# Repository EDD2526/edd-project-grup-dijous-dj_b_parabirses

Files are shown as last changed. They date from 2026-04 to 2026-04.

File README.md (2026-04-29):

# Projecte DJ_B_PARABRISAS

>**Autors:Héctor Rodriguez y MariPaz Carreño
>**Versió: VFinal

----------

## Objectiu

>Crear un pcb para un limpia parabrisas, la cual tendrá control a través de un microcontrolador.
EL objetivo principal es  mantener  la luna del cristal limpia, para ello tenemos un sensor de lluvia que detectará la lluvia, un calefactor para que no se empañe, y bombas de agua que permitan en todo momento limpiar la luna.

## Diagrama de blocs
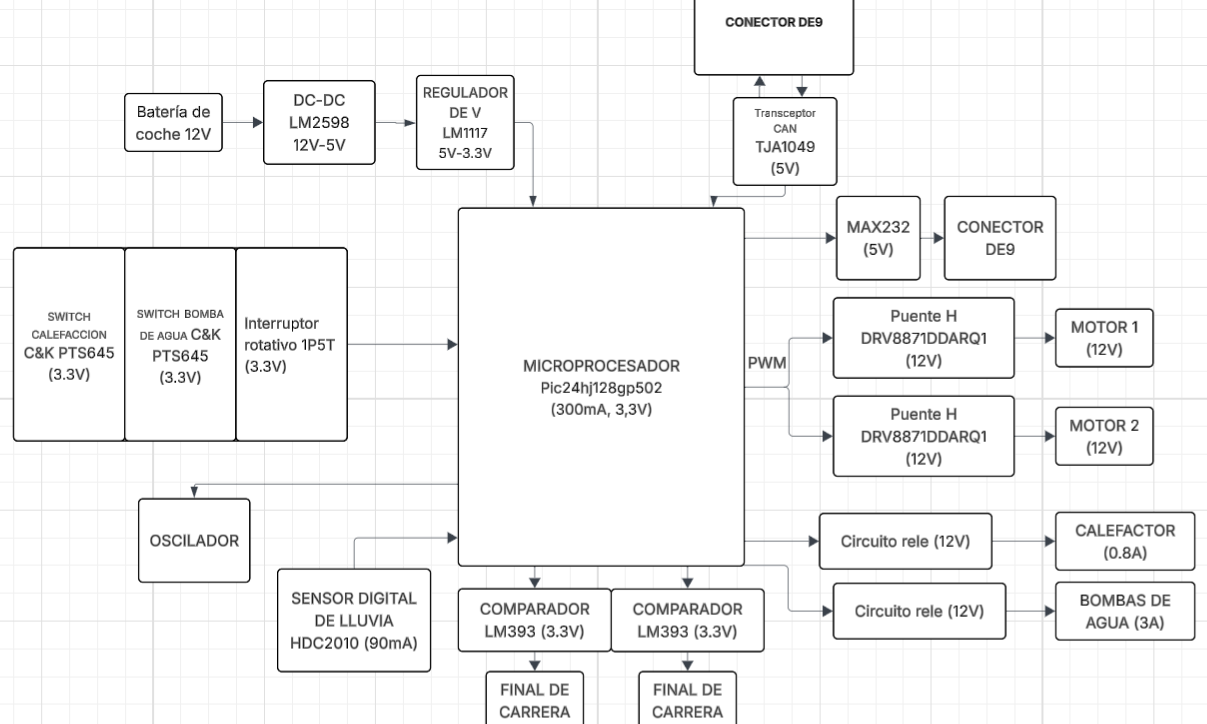
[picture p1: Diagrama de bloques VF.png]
Diagrama de bloques


### Descripció/funcionalitat de cada bloc

  Tenemos el micro en el centro que funcionará como cerebro de todo.
  Como se puede observar uno de los sería la alimentación, consta de un conector que permite meter 12V, después pasa por un convertidor        
  DC-DC, para obtener 5V y por último un regulador para tener un voltaje de 3V.
  Por otro lado tenemos el bloque de potencia: consta de los drivers y motores de los limpiaparabrisas, de los circuitos relé tanto para 
  las bombas, como para el calefactor, y de finales de carrera que permitan volver a su estado inicial.   
  Por último un bloque de conexión/usuario: consta del BUS CAN, este permite la comunicación con otros módulos, el UART, transforma los 
  datos de forma que puedan ser leídos/enviados a un ordenador. También esta el sensor digital de lluvia que detecta cuando hay lluvia y 
  que el motor se ponga en marcha, y por último tendríamos la botonera: sirve para que el usuario acomode el modo del limpiaparabrisas o 
  encienda y apague el calefactor.       
  
-----------

## Requisits / Especificacions

* Alimentació: 12V d’entrada, regulada a 5V i 3.3V
* Microcontrolador: PIC24HJ64GP504
* Regulador buck: LM2596S-5 per obtenir 5V
* Regulador LDO: LM1117DT-3.3 per obtenir 3.3V
* Protecció d’entrada: díode TVS SM6T24A
* Díodes de protecció: D4, D5 i D6 per protegir contra pics inductius
* Comunicació CAN: transceptor TJA1049TK-3
* Comunicació RS232: MAX232
* Oscil·lador: cristall Y1 
* Condensadors de desacoblament: 100nF i 1uF
* Condensadors de filtratge: 680uF, 220uF, 100uF i 10uF
* Resistències: valors diversos per polarització, pull-up, pull-down i limitació de corrent
* Punts de test: TP1, TP2 i TP3

-----------

## Components

| Descripció | Ref | Package | Datasheet | Proveïdor | Preu | Unitats |
|---|---|---|---|---|---|---|
| Capacitor 100nF | C1,C2,C10,C16 | 0805 | ~ | Mouser | — | 4 |
| Capacitor 20pF | C3,C4 | 0805 | ~ | Mouser | — | 2 |
| Capacitor 1uF | C5,C6,C7,C8,C9 | 0805 | ~ | Mouser | — | 5 |
| Capacitor 680uF | C11 | 0805 | ~ | Mouser | — | 1 |
| Capacitor 220uF | C12 | 0805 | ~ | Mouser | — | 1 |
| Capacitor 10uF | C13,C14 | CP Radial D5.0mm P2.50mm | — | Mouser | — | 2 |
| Capacitor 100uF | C15 | CP Radial D5.0mm P2.50mm | — | Mouser | — | 1 |
| Capacitor 10pF | C17 | 0805 | ~ | Mouser | — | 1 |
| Capacitor 100pF | C19 | 0805 | ~ | Mouser | — | 1 |
| LED | D2 | LED 0805 | ~ | Mouser | — | 1 |
| Diodo TVS SM6T24A | D3 | SMB | https://www.st.com/resource/en/datasheet/sm6t.pdf | Mouser | — | 1 |
| Diodo genérico | D4,D5,D6 | 0201 | ~ | Mouser | — | 3 |
| Ferrita | FB1 | LairdTech 28C0236-0JW-10 | ~ | Mouser | — | 1 |
| Final de carrera SPDT | FINALCARRERA1,FINALCARRERA2 | XKB DM1-16UC-1 | ~ | Mouser | — | 2 |
| Conector 1x05 | J1 | PinHeader 1x05 2.54mm | ~ | Mouser | — | 1 |
| Conector DE9 | J2,J3 | DSUB-9 Horizontal | ~ | Mouser | — | 2 |
| Conector 1x02 | J4 | PinHeader 1x02 2.54mm | ~ | Mouser | — | 1 |
| Jumper 3 pines | JP1 | PinHeader 1x03 2.54mm | ~ | Mouser | — | 1 |
| Relé SPST-NO Fujitsu FTR-LYAA005x | K2,K3,K4 | Relay THT Vertical | https://www.fujitsu.com/sg/imagesgig5/ftr-ly.pdf | Mouser | — | 3 |
| Inductor 33uH | L1 | 0603 | ~ | Mouser | — | 1 |
| Motor DC / Bornera salida | M1,M2,M3,M5 | TerminalBlock 2P P5.00mm | ~ | Mouser | — | 4 |
| Transistor NPN MMBT3904 | Q2,Q3,Q4 | SOT-23 | https://www.onsemi.com/pdf/datasheet/pzt3904-d.pdf | Mouser | — | 3 |
| Resistencia 1k | R2,R3,R7,R8 | 0603 | ~ | Mouser | — | 4 |
| Resistencia 4.7k | R4,R13,R14 | 0603 | ~ | Mouser | — | 3 |
| Resistencia 121Ω | R5 | 0603 | ~ | Mouser | — | 1 |
| Resistencia 200Ω | R6 | 0603 | ~ | Mouser | — | 1 |
| Resistencia 10k | R9 | 0603 | ~ | Mouser | — | 1 |
| Resistencia 4.7k | R10 | 0603 | ~ | Mouser | — | 1 |
| Resistencia calefactor | R11 | 2512 | ~ | Mouser | — | 1 |
| Resistencia 60Ω | R12,R17 | 0201 | ~ | Mouser | — | 2 |
| Resistencia 10k | R15,R16 | 0603 | ~ | Mouser | — | 2 |
| Resistencia 7.6k | R18,R22,R23 | 0603 | ~ | Mouser | — | 3 |
| Resistencia 10k | R19,R20,R21 | 0201 | ~ | Mouser | — | 3 |
| Pulsador calefactor | SW1 | Alps SKRK SMD | ~ | Mouser | — | 1 |
| Pulsador bombas | SW2 | Alps SKRK SMD | ~ | Mouser | — | 1 |
| Pulsador | SW3 | Alps SKRK SMD | ~ | Mouser | — | 1 |
| Selector rotativo SP3T | SW5 | NKK NR01 THT | https://www.nkkswitches.com/pdf/NR01%20Rotaries.pdf | Mouser | — | 1 |
| Test point | TP1,TP2,TP3 | Keystone 5015 Micro Mini | ~ | Mouser | — | 3 |
| Regulador LDO 3.3V LM1117DT-3.3 | U1 | TO-252-3 | http://www.ti.com/lit/ds/symlink/lm1117.pdf | Mouser | — | 1 |
| Regulador buck 5V LM2596S-5 | U2 | TO-263-5 | http://www.ti.com/lit/ds/symlink/lm2596.pdf | Mouser | — | 1 |
| Driver motor DRV8871DDA | U3,U7 | HTSOP-8 PowerPAD | http://www.ti.com/lit/ds/symlink/drv8871.pdf | Mouser | — | 2 |
| Microcontrolador PIC24HJ64GP504 | U4 | QFN-44 7x7mm | — | Mouser | — | 1 |
| Sensor humedad/temperatura HDC2080 | U6 | Texas S-PWSON-N6 | http://www.ti.com/lit/ds/symlink/hdc2080.pdf | Mouser | — | 1 |
| Transceptor CAN TJA1049TK-3 | U8 | HVSON-8 | https://www.nxp.com/docs/en/data-sheet/TJA1049.pdf | Mouser | — | 1 |
| Transceptor RS232 MAX232 | U9 | SOIC-16 | http://www.ti.com/lit/ds/symlink/max232.pdf | Mouser | — | 1 |
| Cristal | Y1 | SMD EuroQuartz EQ161 2Pin | ~ | Mouser | — | 1 |

-----------

## Software

### Eines:

  * KiCad 9.0 o superior
  * 

### Configuraci&#243; :

  * 

### Funcionalitats:

  Gestionar el movimiento de las escobillas, el rociado del líquido limpiador mediante dos bombas y el calentamiento del sistema mediante un calefactor.
Cuando el usuario activa el mando, la PCB recibe la señal y enciende el motor del limpiaparabrisas en el modo seleccionado. También puede activar una de las dos bombas, por ejemplo una para el parabrisas delantero y otra para el cristal trasero, enviando líquido limpiador antes o durante el movimiento de las escobillas.
Además, la PCB controla el calefactor, que sirve para calentar el líquido o la zona del sistema de lavado, evitando congelación y mejorando el funcionamiento en bajas temperaturas.

-----------

## Historial de canvis

| Data | Autor | Branch | Versi&#243; | Descripci&#243; |
| --- | --- | --- | --- | --- |
|  28/03/2023 | mlopez | Master | initial commit | Primera versi&#243; d'esquem&#224;tic i selecci&#243; de components |

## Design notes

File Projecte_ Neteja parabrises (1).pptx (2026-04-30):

## Projecte: Neteja parabrises

Hèctor Rodríguez i Marypaz Carreño

## Índice

-Funcionalidad
-Objetivos
-Diagrama de bloques
-Puntos críticos
-Componentes
-PCB, Esquemático, Visión 3D
-Presupuesto

## Funcionalidad

Gestionar el movimiento de las escobillas, el rociado del líquido limpiador mediante dos bombas y el calentamiento del sistema mediante un calefactor.
Cuando el usuario activa el mando, la PCB recibe la señal y enciende el motor del limpiaparabrisas en el modo seleccionado. También puede activar una de las dos bombas, por ejemplo una para el parabrisas delantero y otra para el cristal trasero, enviando líquido limpiador antes o durante el movimiento de las escobillas.
Además, la PCB controla el calefactor, que sirve para calentar el líquido o la zona del sistema de lavado, evitando congelación y mejorando el funcionamiento en bajas temperaturas.

## Objetivos

Mantener las lunas del coche todo lo limpias posible para que el conductor pueda tener una buen visibilidad.

## Diagrama de bloques


## Puntos críticos

- Planos de alimentacion.
- Cantidad de pines para switches.
- Routing de la parte de potencia.
- Dimensiones de pista, debido a la alta corriente.

## Componentes

- Microcontrolador PIC24HJ64GP504
- Regulador buck LM2596S-5
- Regulador LDO LM1117DT-3.3
- Driver de motor DRV8871DDA
- Transceptor CAN TJA1049TK-3
- Transceptor RS232 MAX232
- Sensor HDC2080
- Relés Fujitsu FTR-LYAA005x
- Transistores MMBT3904
- Diodo TVS SM6T24A
- Diodos genéricos
- LED

- Ferrita (Ferrite Bead)
- Inductor 33uH
- Cristal
- Resistencias
- Resistencia calefactor
- Condensadores
- Pulsadores
- Selector rotativo
- Finales de carrera
- Conectores
- Jumper
- Test points
- Borneras / terminales

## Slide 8

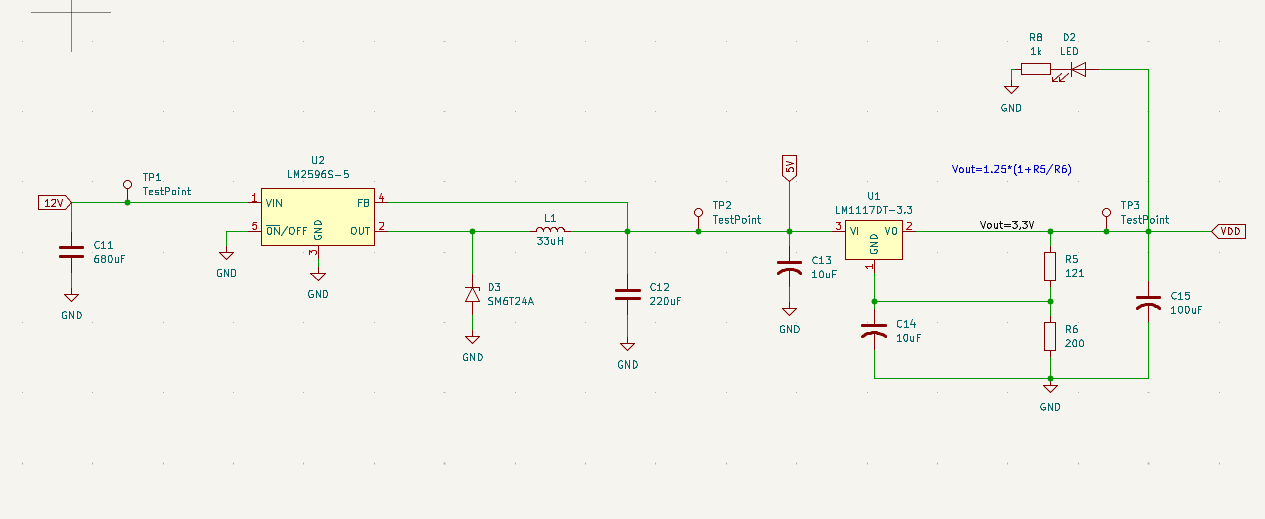
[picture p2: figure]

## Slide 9

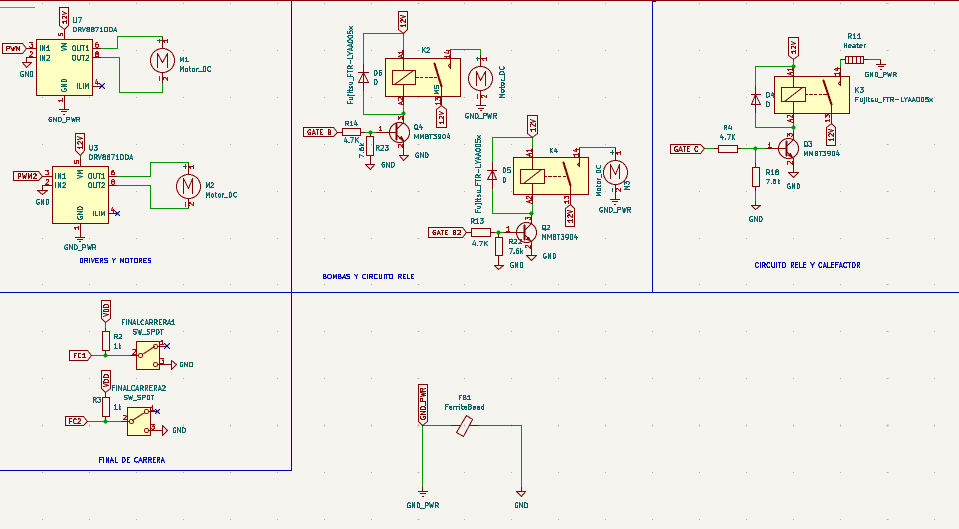
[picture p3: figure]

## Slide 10

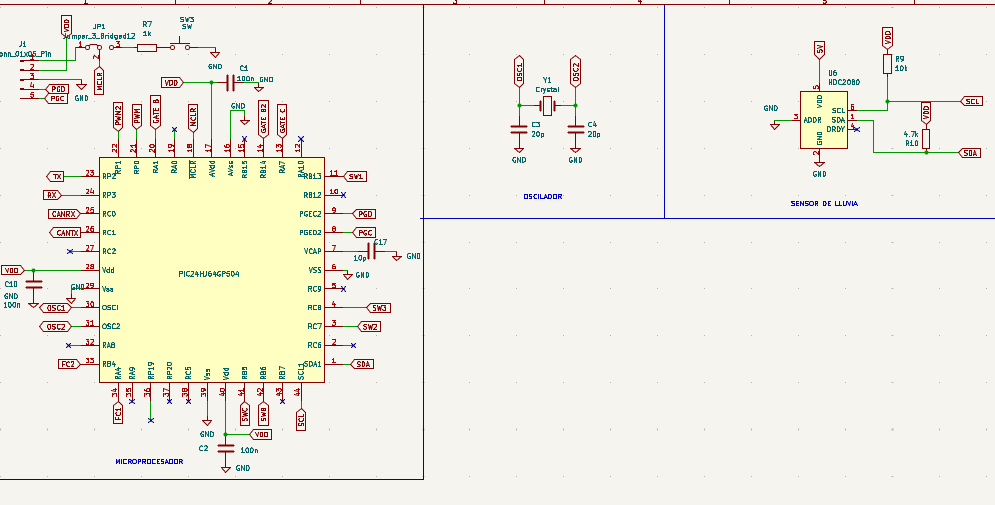
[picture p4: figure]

## BOTONERA

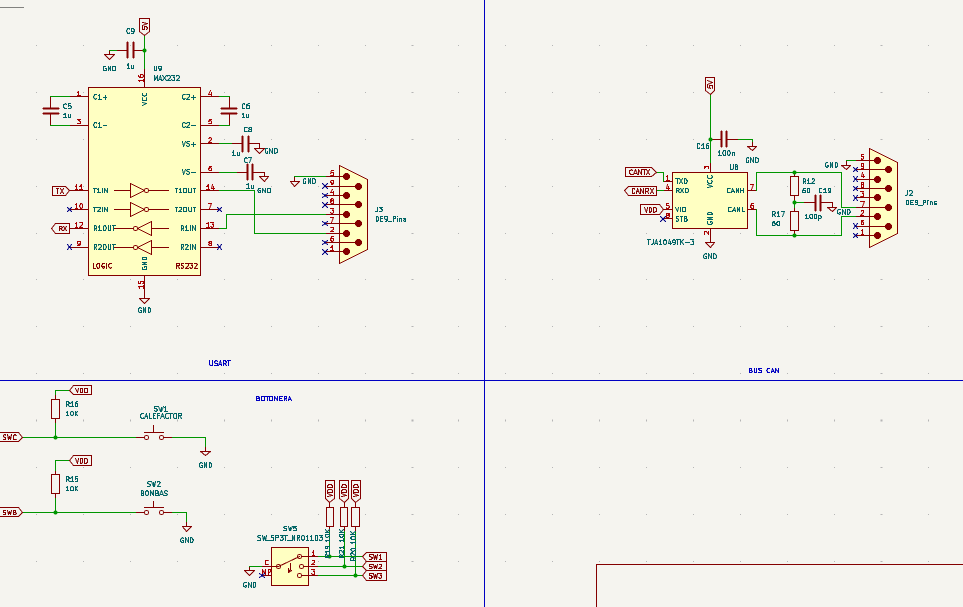
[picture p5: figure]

## PCB

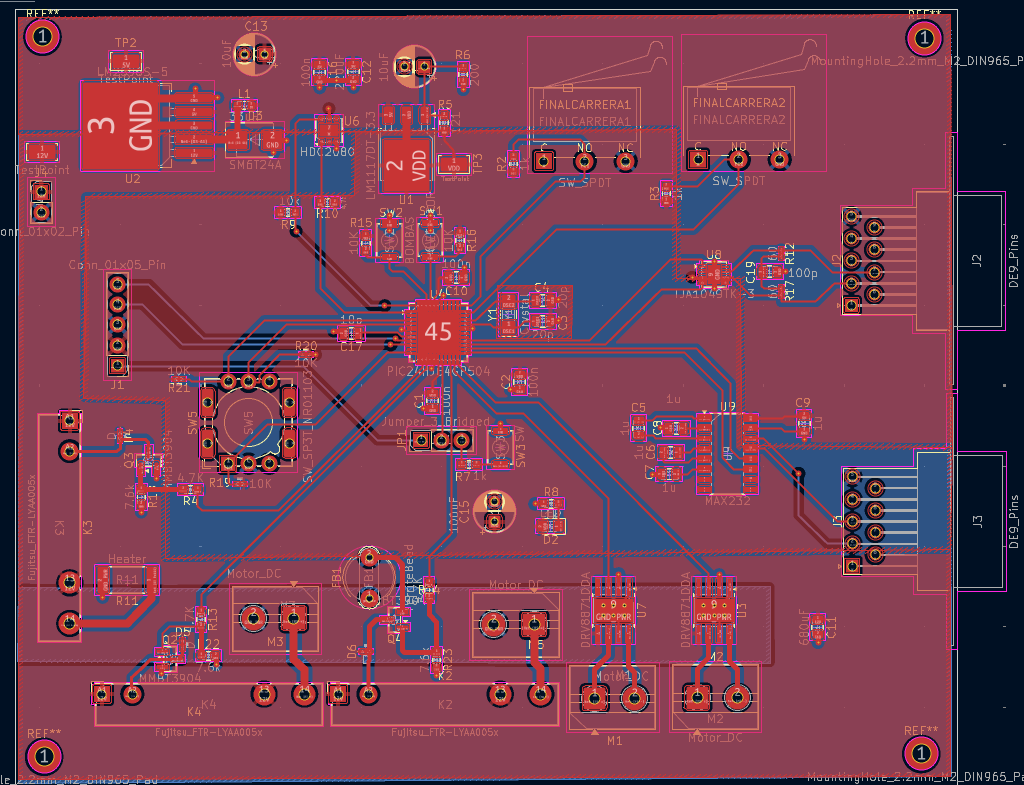
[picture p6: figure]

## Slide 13

TOP

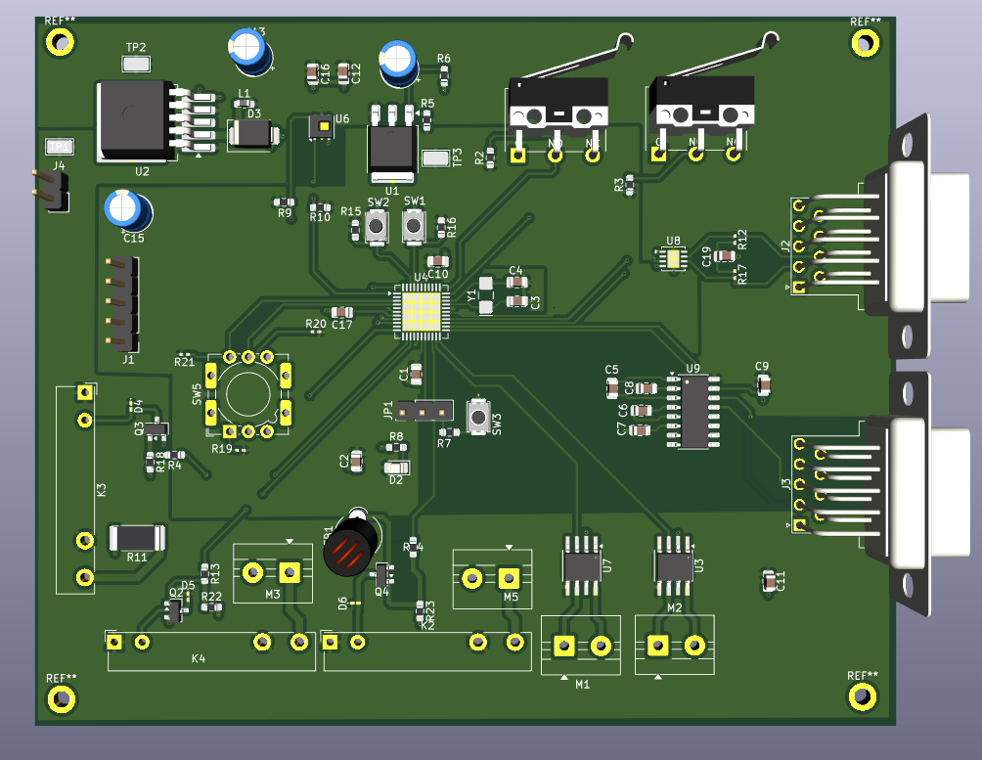
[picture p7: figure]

BOTTOM

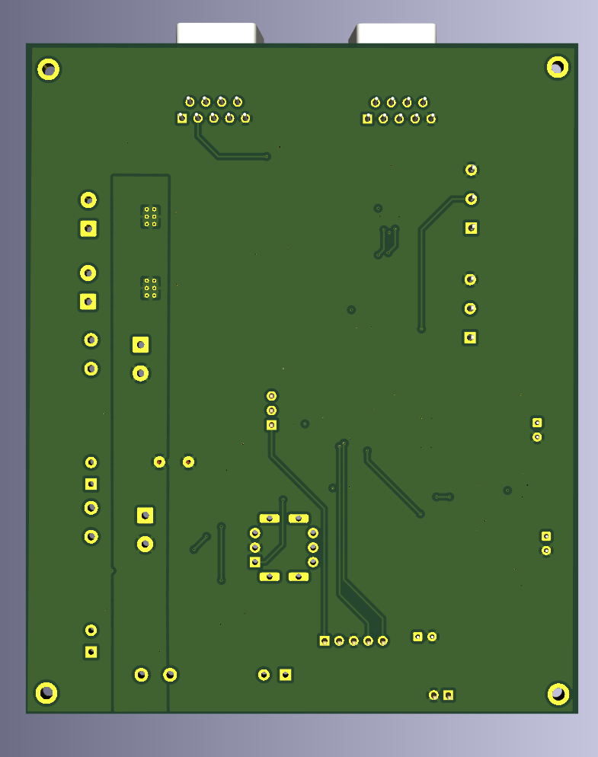
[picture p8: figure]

## Gerbers

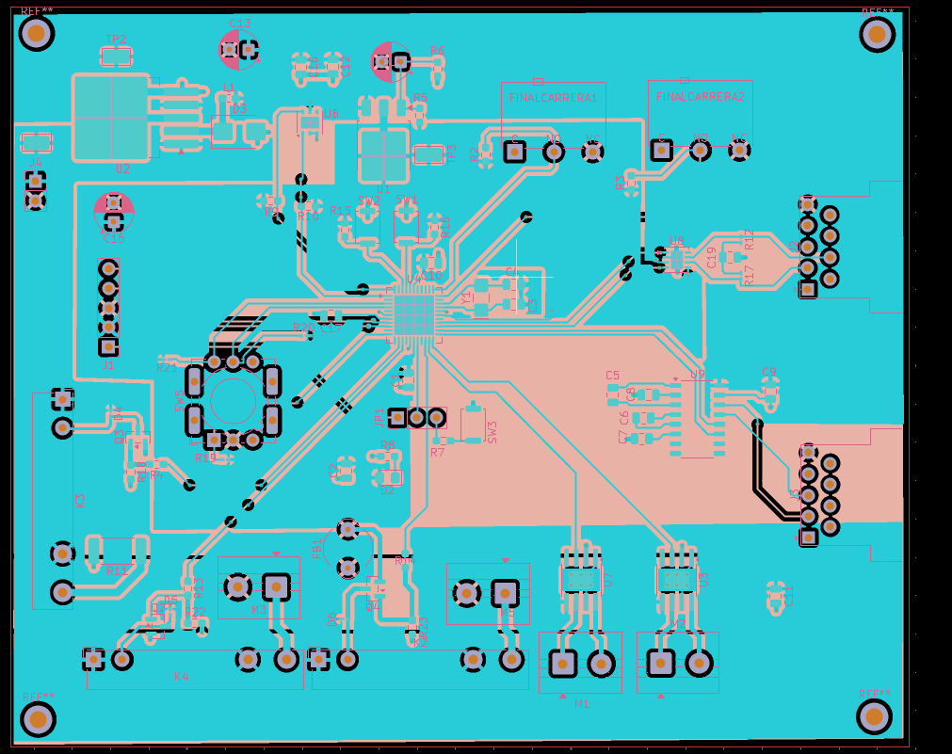
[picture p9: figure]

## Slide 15

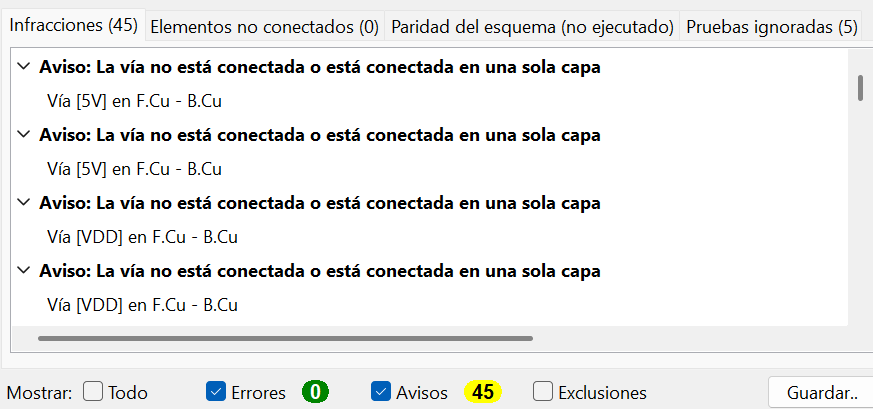
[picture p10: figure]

## Pressupost

Excel:

https://docs.google.com/spreadsheets/d/1Wet3hvXIElzK6eD7wXQeXx7nQDkMxnmVZ5MyvcNb8l4/edit?usp=sharing

Unitari: (x10)=>23.43$, (x50)=>21.8$, (x1000)=>13.14$, (x20000)=>23.59$
Total: (x10)=>234.35$, (x50)=>1090$, (x1000)=>13194$, (x20000)=>471894$

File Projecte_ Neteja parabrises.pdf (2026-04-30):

# Projecte: Neteja parabrises

Hèctor Rodríguez i Marypaz Carreño

Índice | -Funcionalidad
| -Objetivos
| -Diagrama de bloques
| -Puntos críticos
| -Componentes
| -PCB, Esquemático, Visión 3D
| -Presupuesto

# Funcionalidad

Gestionar el movimiento de las escobillas, el rociado del líquido limpiador mediante dos bombas y el calentamiento del sistema mediante un calefactor.

Cuando el usuario activa el mando, la PCB recibe la señal y enciende el motor del limpiaparabrisas en el modo seleccionado. También puede activar una de las dos bombas, por ejemplo una para el parabrisas delantero y otra para el cristal trasero, enviando líquido limpiador antes o durante el movimiento de las escobillas.

Además, la PCB controla el calefactor, que sirve para calentar el líquido o la zona del sistema de lavado, evitando congelación y mejorando el funcionamiento en bajas temperaturas.

# Objetivos

Mantener las lunas del coche todo lo limpias posible para que el conductor pueda tener una buen visibilidad.

# Diagrama de bloques

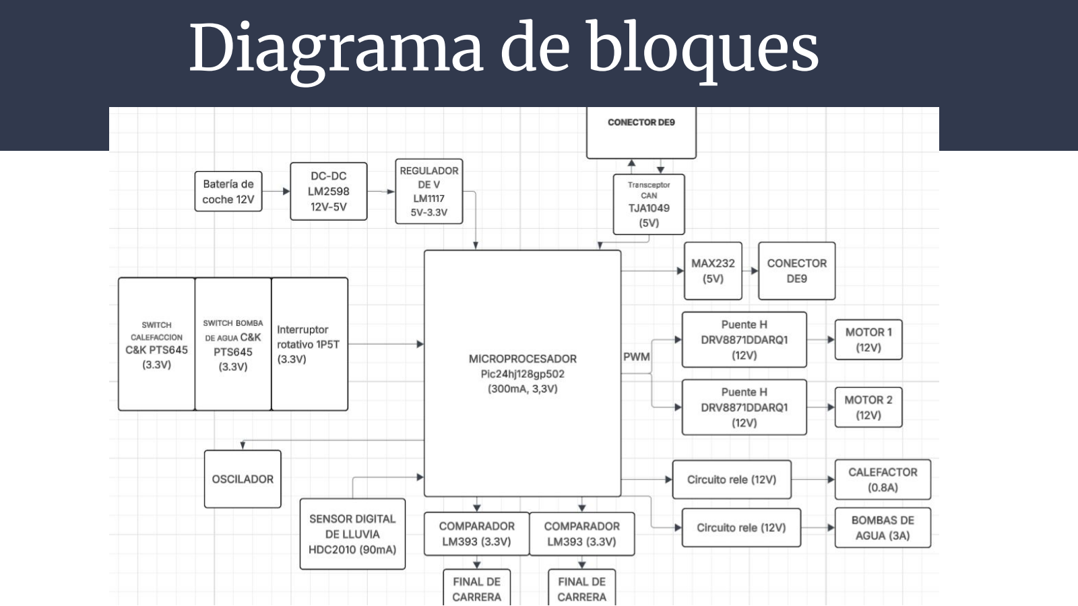
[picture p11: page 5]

# Puntos críticos

- Planos de alimentacion.
- Cantidad de pines para switches.
- Routing de la parte de potencia.
- Dimensiones de pista, debido a la alta corriente.

# Componentes

- Microcontrolador
PIC24HJ64GP504
- Regulador buck LM2596S-5
- Regulador LDO LM1117DT-3.3
- Driver de motor DRV8871DDA
- Transceptor CAN TJA1049TK-3
- Transceptor RS232 MAX232
- Sensor HDC2080
- Relés Fujitsu FTR-LYAA005x
- Transistores MMBT3904
- Diodo TVS SM6T24A
- Diodos genéricos
- LED
- Ferrita (Ferrite Bead)
- Inductor 33uH
- Cristal
- Resistencias
- Resistencia calefactor
- Condensadores
- Pulsadores
- Selector rotativo
- Finales de carrera
- Conectores
- Jumper
- Test points
- Borneras / terminales

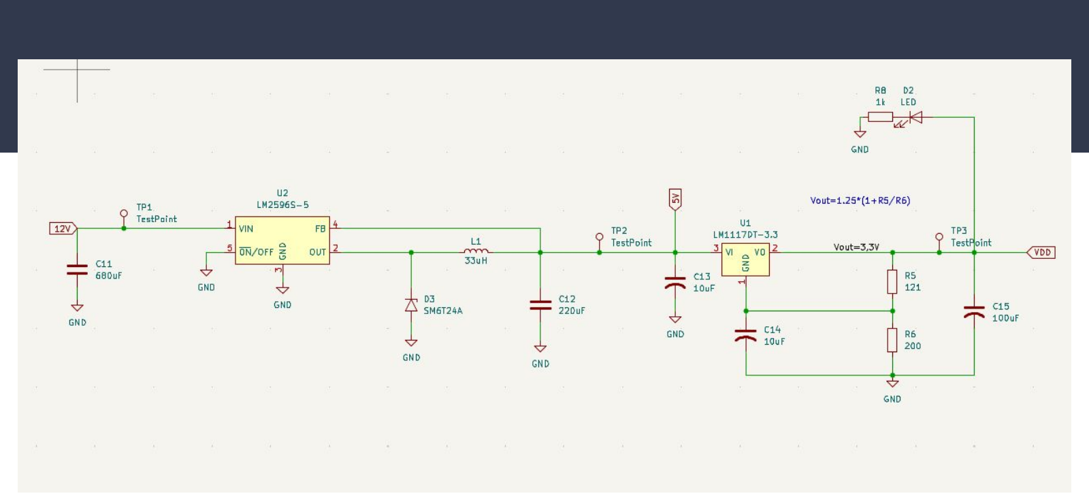
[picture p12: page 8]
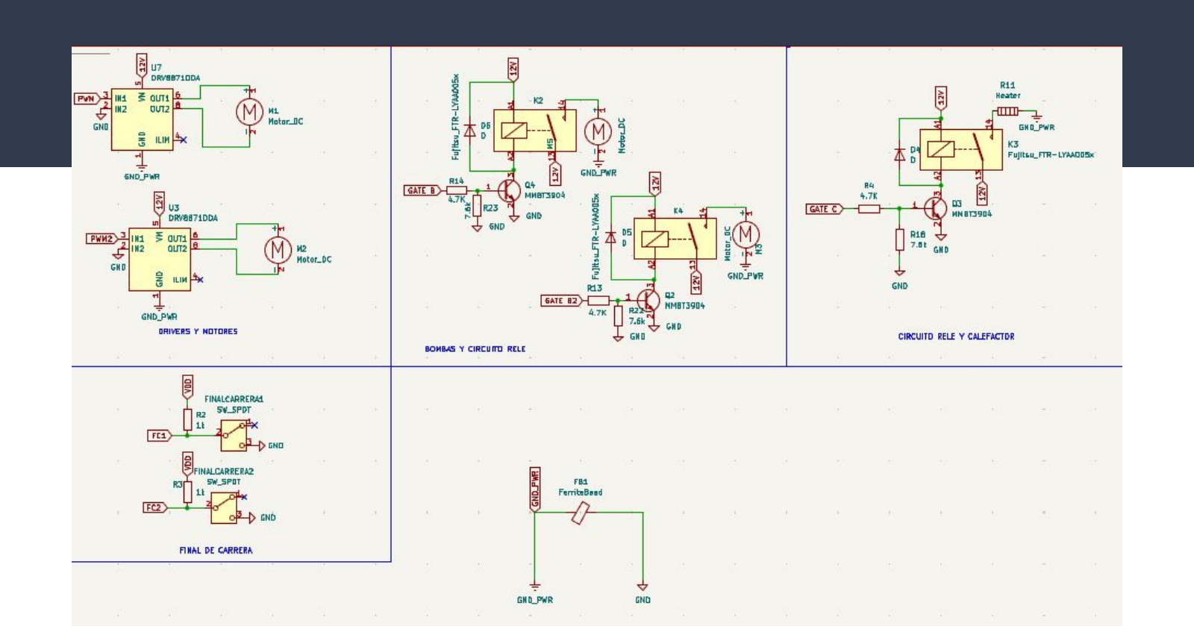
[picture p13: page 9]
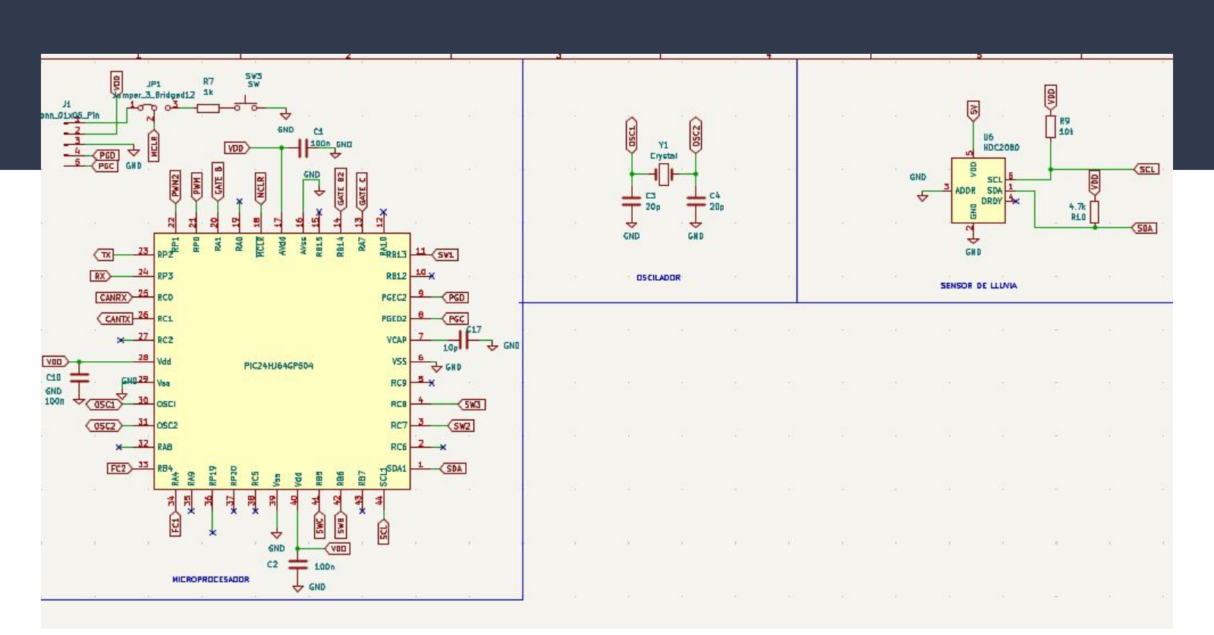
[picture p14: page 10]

## BOTONERA

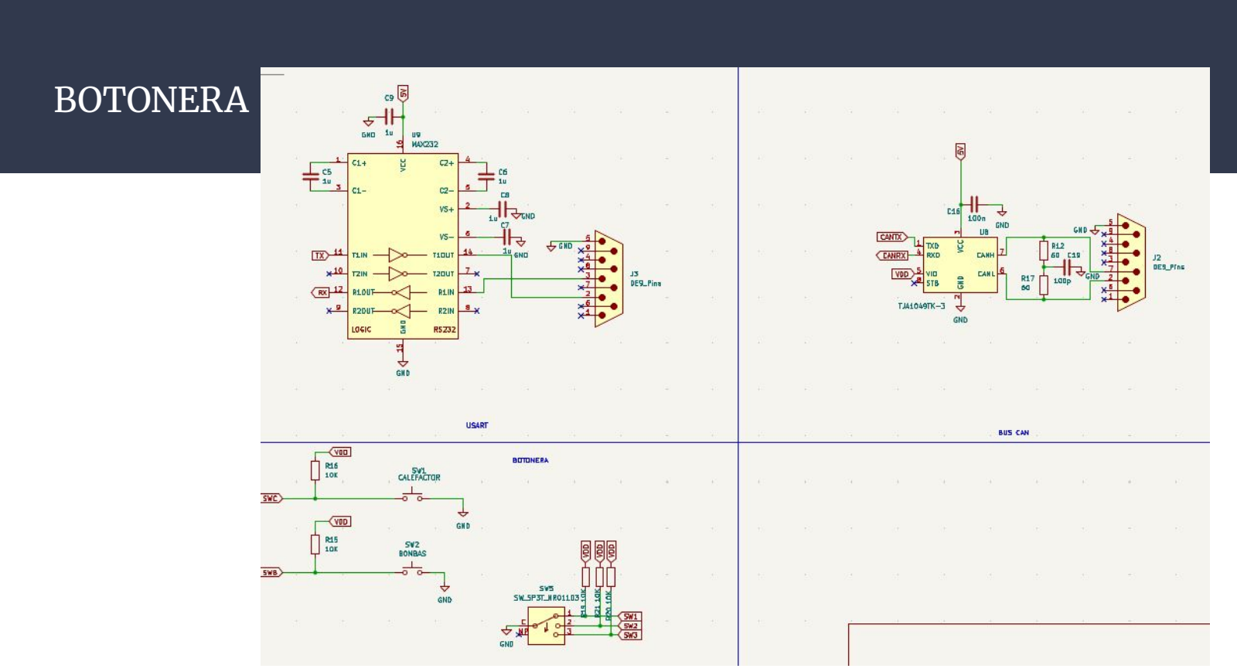
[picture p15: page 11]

# PCB

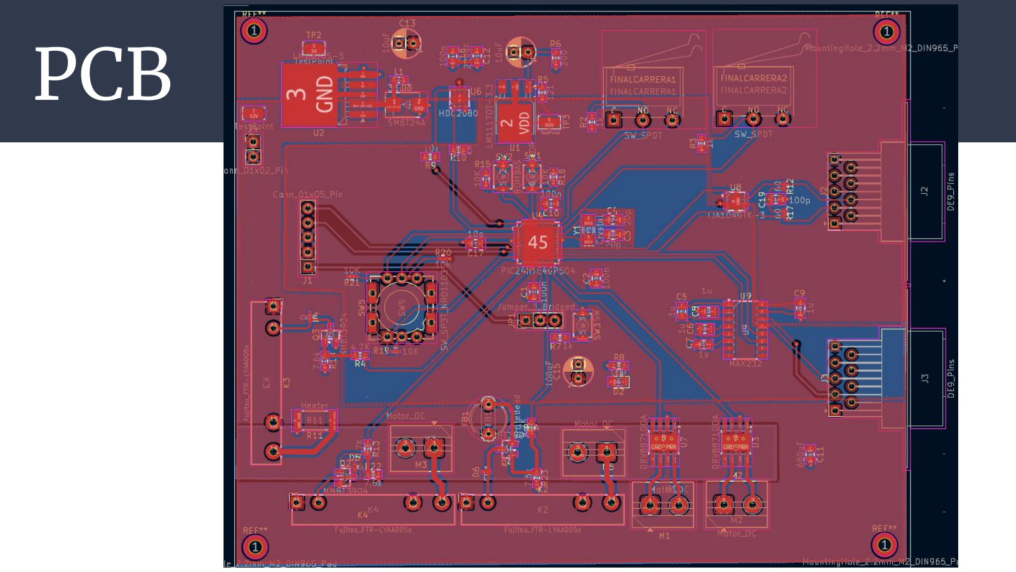
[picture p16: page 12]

TOP | BOTTOM

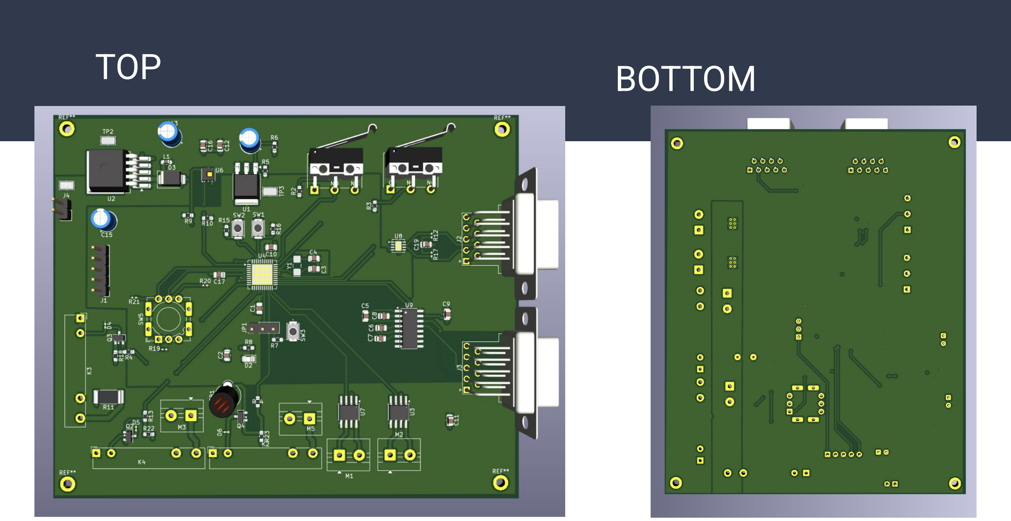
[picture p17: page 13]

# Gerbers

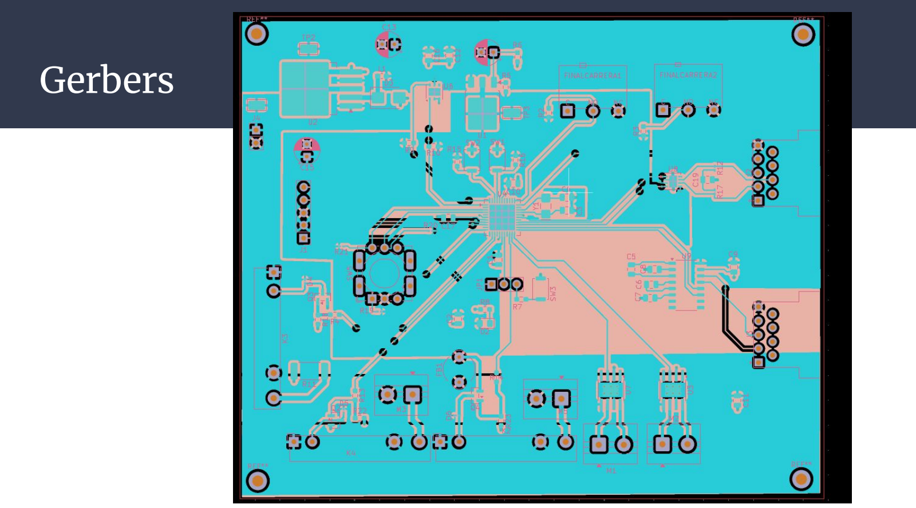
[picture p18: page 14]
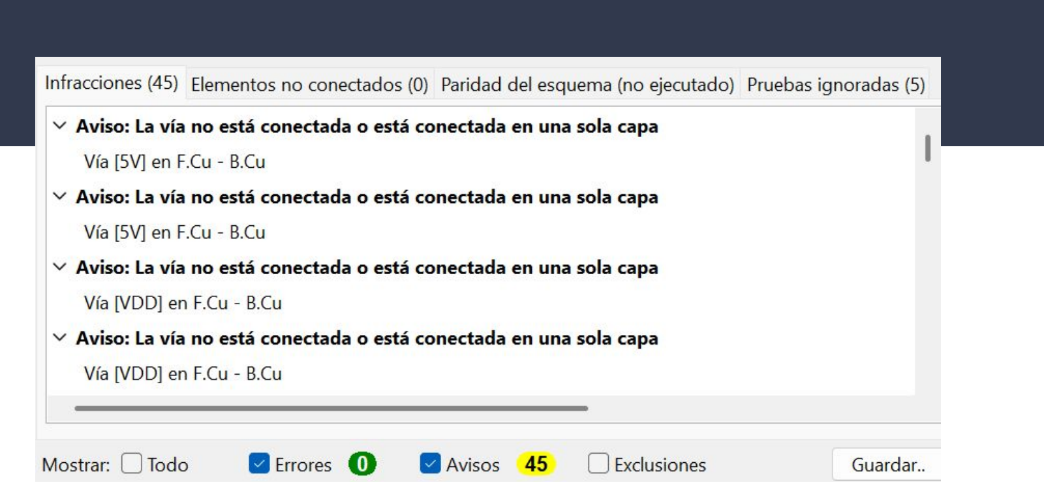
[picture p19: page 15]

# Pressupost

### Unitari: (x10)=>23.43$, (x50)=>21.8$, (x1000)=>13.14$, (x20000)=>23.59$

### Total: (x10)=>234.35$, (x50)=>1090$, (x1000)=>13194$, (x20000)=>471894$

https://docs.google.com/spreadsheets/d/1Wet3hvXIElzK6eD7wXQeXx7nQDkMxnmVZ5MyvcNb8l4/edit?usp=sharing (https://docs.google.com/spreadsheets/d/1Wet3hvXIElzK6eD7wXQeXx7nQDkMxnmVZ5MyvcNb8l4/edit?usp=sharing)

### Excel:

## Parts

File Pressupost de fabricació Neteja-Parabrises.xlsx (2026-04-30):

x10 | Preu unitari ($) | Preu total ($) | Referència | x50 | Preu unitari ($) | Preu total ($) | Referència | x1000 | Preu unitari ($) | Preu total ($) | Referència | x20000 | Preu unitari ($) | Preu total ($) | Referència
C1 | 0.0392 | 0.392 | https://www.unikeyic.com/products/ceramic-capacitors/fs051c104k4z2a/19464201.html | C1 | 0.0314 | 1.57 | https://www.unikeyic.com/products/ceramic-capacitors/fs051c104k4z2a/19464201.html | C1 | 0.0251 | 25.1 | https://www.unikeyic.com/products/ceramic-capacitors/cl21f104zbcnnnc/18680341.html | C1 | 0.0251 | 502 | https://www.unikeyic.com/products/ceramic-capacitors/cl21f104zbcnnnc/18680341.html
C2 | 0.0392 | 0.392 | https://www.unikeyic.com/products/ceramic-capacitors/fs051c104k4z2a/19464201.html | C2 | 0.0314 | 1.57 | https://www.unikeyic.com/products/ceramic-capacitors/fs051c104k4z2a/19464201.html | C2 | 0.0251 | 25.1 | https://www.unikeyic.com/products/ceramic-capacitors/cl21f104zbcnnnc/18680341.html | C2 | 0.0251 | 502 | https://www.unikeyic.com/products/ceramic-capacitors/cl21f104zbcnnnc/18680341.html
C3 | 0.245 | 2.45 | https://www.unikeyic.com/products/ceramic-capacitors/gqm2195c2e200jb12d/9406125.html | C3 | 0.245 | 12.25 | https://www.unikeyic.com/products/ceramic-capacitors/gqm2195c2e200jb12d/9406125.html | C3 | 0.0205 | 20.5 | https://www.unikeyic.com/products/ceramic-capacitors/c0805c200k8hactu/10609661.html | C3 | 0.007 | 140 | https://www.unikeyic.com/products/ceramic-capacitors/tcc0805cog200j500bt/21239242.html
C4 | 0.245 | 2.45 | https://www.unikeyic.com/products/ceramic-capacitors/gqm2195c2e200jb12d/9406125.html | C4 | 0.245 | 12.25 | https://www.unikeyic.com/products/ceramic-capacitors/gqm2195c2e200jb12d/9406125.html | C4 | 0.0205 | 20.5 | https://www.unikeyic.com/products/ceramic-capacitors/c0805c200k8hactu/10609661.html | C4 | 0.007 | 140 | https://www.unikeyic.com/products/ceramic-capacitors/tcc0805cog200j500bt/21239242.html
C5 | 0.0173 | 0.173 | https://www.unikeyic.com/products/ceramic-capacitors/cc0805mry5v7bb105/7588510.html | C5 | 0.0085 | 0.425 | https://www.unikeyic.com/products/ceramic-capacitors/ac0805kkx7r5bb105/20753629.html | C5 | 0.0073 | 7.3 | https://www.unikeyic.com/products/ceramic-capacitors/ac0805kkx7r5bb105/20753629.html | C5 | 0.0133 | 266 | https://www.unikeyic.com/products/ceramic-capacitors/cl21b105kofnfne/6708661.html
C6 | 0.0173 | 0.173 | https://www.unikeyic.com/products/ceramic-capacitors/cc0805mry5v7bb105/7588510.html | C6 | 0.0085 | 0.425 | https://www.unikeyic.com/products/ceramic-capacitors/ac0805kkx7r5bb105/20753629.html | C6 | 0.0073 | 7.3 | https://www.unikeyic.com/products/ceramic-capacitors/ac0805kkx7r5bb105/20753629.html | C6 | 0.0133 | 266 | https://www.unikeyic.com/products/ceramic-capacitors/cl21b105kofnfne/6708661.html
C7 | 0.0173 | 0.173 | https://www.unikeyic.com/products/ceramic-capacitors/cc0805mry5v7bb105/7588510.html | C7 | 0.0085 | 0.425 | https://www.unikeyic.com/products/ceramic-capacitors/ac0805kkx7r5bb105/20753629.html | C7 | 0.0073 | 7.3 | https://www.unikeyic.com/products/ceramic-capacitors/ac0805kkx7r5bb105/20753629.html | C7 | 0.0133 | 266 | https://www.unikeyic.com/products/ceramic-capacitors/cl21b105kofnfne/6708661.html
C8 | 0.0173 | 0.173 | https://www.unikeyic.com/products/ceramic-capacitors/cc0805mry5v7bb105/7588510.html | C8 | 0.0085 | 0.425 | https://www.unikeyic.com/products/ceramic-capacitors/ac0805kkx7r5bb105/20753629.html | C8 | 0.0073 | 7.3 | https://www.unikeyic.com/products/ceramic-capacitors/ac0805kkx7r5bb105/20753629.html | C8 | 0.0133 | 266 | https://www.unikeyic.com/products/ceramic-capacitors/cl21b105kofnfne/6708661.html
C9 | 0.0173 | 0.173 | https://www.unikeyic.com/products/ceramic-capacitors/cc0805mry5v7bb105/7588510.html | C9 | 0.0085 | 0.425 | https://www.unikeyic.com/products/ceramic-capacitors/ac0805kkx7r5bb105/20753629.html | C9 | 0.0073 | 7.3 | https://www.unikeyic.com/products/ceramic-capacitors/ac0805kkx7r5bb105/20753629.html | C9 | 0.0133 | 266 | https://www.unikeyic.com/products/ceramic-capacitors/cl21b105kofnfne/6708661.html
C10 | 0.0392 | 0.392 | https://www.unikeyic.com/products/ceramic-capacitors/fs051c104k4z2a/19464201.html | C10 | 0.0314 | 1.57 | https://www.unikeyic.com/products/ceramic-capacitors/fs051c104k4z2a/19464201.html | C10 | 0.0289 | 28.9 | https://www.unikeyic.com/products/ceramic-capacitors/cl21f104zbcnnnc/18680341.html | C10 | 0.0251 | 502 | https://www.unikeyic.com/products/ceramic-capacitors/cl21f104zbcnnnc/18680341.html
C11 | 0.3301 | 3.301 | https://www.unikeyic.com/products/ceramic-capacitors/sr215a681kaatr1/10381887.html | C11 | 0.3301 | 16.505 | https://www.unikeyic.com/products/ceramic-capacitors/sr215a681kaatr1/10381887.html | C11 | 0.0561 | 56.1 | https://www.unikeyic.com/products/ceramic-capacitors/0603zc681kat2a/7394239.html | C11 | 0.0198 | 396 | https://www.unikeyic.com/products/ceramic-capacitors/grm1885c1h681fa01d/20994921.html
C12 | 0.3512 | 3.512 | https://www.unikeyic.com/products/ceramic-capacitors/grm31cr60g227me11l/19408997.html | C12 | 0.2953 | 14.765 | https://www.unikeyic.com/products/ceramic-capacitors/grm31cr60g227me11l/19408997.html | C12 | 0.2436 | 243.6 | https://www.unikeyic.com/products/ceramic-capacitors/grm31cr60g227me11l/19408997.html | C12 | 0.2104 | 4208 | https://www.unikeyic.com/products/ceramic-capacitors/c1206x5r227m6r3nt/1005581067.html
C13 | 0.1428 | 1.428 | https://www.unikeyic.com/products/ceramic-capacitors/msasj21gab7106ktna01/14967858.html | C13 | 0.1428 | 7.14 | https://www.unikeyic.com/products/ceramic-capacitors/msasj21gab7106ktna01/14967858.html | C13 | 0.0566 | 56.6 | https://www.unikeyic.com/products/ceramic-capacitors/grm21bc80j106me19l/10240704.html | C13 | 0.0052 | 104 | https://www.unikeyic.com/products/ceramic-capacitors/c0805x5r106k100ns/30244845.html
C14 | 0.1428 | 1.428 | https://www.unikeyic.com/products/ceramic-capacitors/msasj21gab7106ktna01/14967858.html | C14 | 0.1428 | 7.14 | https://www.unikeyic.com/products/ceramic-capacitors/msasj21gab7106ktna01/14967858.html | C14 | 0.0566 | 56.6 | https://www.unikeyic.com/products/ceramic-capacitors/grm21bc80j106me19l/10240704.html | C14 | 0.0052 | 104 | https://www.unikeyic.com/products/ceramic-capacitors/c0805x5r106k100ns/30244845.html
C15 | 0.1792 | 1.792 | https://www.unikeyic.com/products/ceramic-capacitors/grm21br60j107me15k/19293684.html | C15 | 0.1338 | 6.69 | https://www.unikeyic.com/products/ceramic-capacitors/grm21br60j107me15k/19293684.html | C15 | 0.1145 | 114.5 | https://www.unikeyic.com/products/ceramic-capacitors/grm21br60j107me15k/19293684.html | C15 | 0.1379 | 2758 | https://www.unikeyic.com/products/ceramic-capacitors/grm21br60g107me11k/7312965.html
C16 | 0.0392 | 0.392 | https://www.unikeyic.com/products/ceramic-capacitors/fs051c104k4z2a/19464201.html | C16 | 0.0314 | 1.57 | https://www.unikeyic.com/products/ceramic-capacitors/fs051c104k4z2a/19464201.html | C16 | 0.0289 | 28.9 | https://www.unikeyic.com/products/ceramic-capacitors/cl21f104zbcnnnc/18680341.html | C16 | 0.0251 | 502 | https://www.unikeyic.com/products/ceramic-capacitors/cl21f104zbcnnnc/18680341.html
C17 | 0.0041 | 0.041 | https://www.unikeyic.com/products/ceramic-capacitors/cga0805c0g100j500ht/857497660.html | C17 | 0.0032 | 0.16 | https://www.unikeyic.com/products/ceramic-capacitors/cga0805c0g100j500ht/857497660.html | C17 | 0.0097 | 9.7 | https://www.unikeyic.com/products/ceramic-capacitors/c0805c100j5gac7800/6769988.html | C17 | 0.0052 | 104 | https://www.unikeyic.com/products/ceramic-capacitors/ac0805jrnpo9bn100/9246806.html
C19 | 0.0181 | 0.181 | https://www.unikeyic.com/products/ceramic-capacitors/08055c101jat2a/20491657.html | C19 | 0.0181 | 0.905 | https://www.unikeyic.com/products/ceramic-capacitors/08055c101jat2a/20491657.html | C19 | 0.0153 | 15.3 | https://www.unikeyic.com/products/ceramic-capacitors/c0805x7r101-101jnp/21187320.html | C19 | 0.0153 | 306 | https://www.unikeyic.com/products/ceramic-capacitors/c0805x7r101-101jnp/21187320.html
D2 | 0.0123 | 0.123 | https://www.unikeyic.com/products/led/ncd0805r1/13242756.html | D2 | 0.0122 | 0.61 | https://www.unikeyic.com/products/led/ncd0805o1/30976298.html | D2 | 0.0104 | 10.4 | https://www.unikeyic.com/products/led/ncd0805o1/30976298.html | D2 | 0.0024 | 48 | https://www.unikeyic.com/products/led/aav-004-r000/1000194485.html
D3 | 1.0792 | 10.792 | https://www.unikeyic.com/products/current-stabilizing-diodes/tlp548j-tp1-f/8251332.html | D3 | 0.8997 | 44.985 | https://www.unikeyic.com/products/current-stabilizing-diodes/tlp548j-tp1-f/8251332.html | D3 | 0.0475 | 47.5 | https://www.unikeyic.com/products/current-stabilizing-diodes/lm317/871062347.html | D3 | 0.0443 | 886 | https://www.unikeyic.com/products/current-stabilizing-diodes/lm317/871062347.html
D4 | 1.0792 | 10.792 | https://www.unikeyic.com/products/current-stabilizing-diodes/tlp548j-tp1-f/8251332.html | D4 | 0.8997 | 44.985 | https://www.unikeyic.com/products/current-stabilizing-diodes/tlp548j-tp1-f/8251332.html | D4 | 0.0475 | 47.5 | https://www.unikeyic.com/products/current-stabilizing-diodes/lm317/871062347.html | D4 | 0.0443 | 886 | https://www.unikeyic.com/products/current-stabilizing-diodes/lm317/871062347.html
D5 | 1.0792 | 10.792 | https://www.unikeyic.com/products/current-stabilizing-diodes/tlp548j-tp1-f/8251332.html | D5 | 0.8997 | 44.985 | https://www.unikeyic.com/products/current-stabilizing-diodes/tlp548j-tp1-f/8251332.html | D5 | 0.0475 | 47.5 | https://www.unikeyic.com/products/current-stabilizing-diodes/lm317/871062347.html | D5 | 0.0443 | 886 | https://www.unikeyic.com/products/current-stabilizing-diodes/lm317/871062347.html
D6 | 1.0792 | 10.792 | https://www.unikeyic.com/products/current-stabilizing-diodes/tlp548j-tp1-f/8251332.html | D6 | 0.8997 | 44.985 | https://www.unikeyic.com/products/current-stabilizing-diodes/tlp548j-tp1-f/8251332.html | D6 | 0.0475 | 47.5 | https://www.unikeyic.com/products/current-stabilizing-diodes/lm317/871062347.html | D6 | 0.0443 | 886 | https://www.unikeyic.com/products/current-stabilizing-diodes/lm317/871062347.html
FB1 | 1.0032 | 10.032 | https://www.unikeyic.com/products/magnetic-beads/28c0236-0bw-10/28061261.html | FB1 | 1.0032 | 50.16 | https://www.unikeyic.com/products/magnetic-beads/28c0236-0bw-10/28061261.html | FB1 | 0.0507 | 50.7 | https://www.unikeyic.com/products/magnetic-beads/fba04ha450bb-00/23676552.html | FB1 | 0.0396 | 792 | https://www.unikeyic.com/products/magnetic-beads/fba04ha450bb-00/23676552.html
FINALCARRERA1 | 0.1291 | 1.291 | https://www.unikeyic.com/products/pushbutton-switches/tk-6800-1/30582253.html | FINALCARRERA1 | 0.1062 | 5.31 | https://www.unikeyic.com/products/pushbutton-switches/tk-6800-1/30582253.html | FINALCARRERA1 | 0.1003 | 100.3 | https://www.unikeyic.com/products/pushbutton-switches/xkb8080-z/29657719.html | FINALCARRERA1 | 0.6609 | 13218 | https://www.unikeyic.com/products/pushbutton-switches/tmg1-01/30003257.html
FINALCARRERA2 | 0.1291 | 1.291 | https://www.unikeyic.com/products/pushbutton-switches/tk-6800-1/30582253.html | FINALCARRERA2 | 0.1062 | 5.31 | https://www.unikeyic.com/products/pushbutton-switches/tk-6800-1/30582253.html | FINALCARRERA2 | 0.1003 | 100.3 | https://www.unikeyic.com/products/pushbutton-switches/xkb8080-z/29657719.html | FINALCARRERA2 | 0.6609 | 13218 | https://www.unikeyic.com/products/pushbutton-switches/tmg1-01/30003257.html
J1 | 0.0542 | 0.542 | https://www.unikeyic.com/products/blade-connector-housings/0351510210/34594861.html | J1 | 0.0437 | 2.185 | https://www.unikeyic.com/products/blade-connector-housings/0351510210/34594861.html | J1 | 0.036 | 36 | https://www.unikeyic.com/products/blade-connector-housings/0351500200/18454904.html | J1 | 0.0385 | 770 | https://www.unikeyic.com/products/blade-connector-housings/351500100/19714676.html
J2 | 0.0542 | 0.542 | https://www.unikeyic.com/products/blade-connector-housings/0351510210/34594861.html | J2 | 0.0437 | 2.185 | https://www.unikeyic.com/products/blade-connector-housings/0351510210/34594861.html | J2 | 0.036 | 36 | https://www.unikeyic.com/products/blade-connector-housings/0351500200/18454904.html | J2 | 0.0385 | 770 | https://www.unikeyic.com/products/blade-connector-housings/351500100/19714676.html
J3 | 0.0542 | 0.542 | https://www.unikeyic.com/products/blade-connector-housings/0351510210/34594861.html | J3 | 0.0437 | 2.185 | https://www.unikeyic.com/products/blade-connector-housings/0351510210/34594861.html | J3 | 0.036 | 36 | https://www.unikeyic.com/products/blade-connector-housings/0351500200/18454904.html | J3 | 0.0385 | 770 | https://www.unikeyic.com/products/blade-connector-housings/351500100/19714676.html
J4 | 0.0542 | 0.542 | https://www.unikeyic.com/products/blade-connector-housings/0351510210/34594861.html | J4 | 0.0437 | 2.185 | https://www.unikeyic.com/products/blade-connector-housings/0351510210/34594861.html | J4 | 0.036 | 36 | https://www.unikeyic.com/products/blade-connector-housings/0351500200/18454904.html | J4 | 0.0385 | 770 | https://www.unikeyic.com/products/blade-connector-housings/351500100/19714676.html
JP1 | 0.0542 | 0.542 | https://www.unikeyic.com/products/blade-connector-housings/0351510210/34594861.html | JP1 | 0.0437 | 2.185 | https://www.unikeyic.com/products/blade-connector-housings/0351510210/34594861.html | JP1 | 0.036 | 36 | https://www.unikeyic.com/products/blade-connector-housings/0351500200/18454904.html | JP1 | 0.0385 | 770 | https://www.unikeyic.com/products/blade-connector-housings/351500100/19714676.html
K2 | 0.3014 | 3.014 | https://www.unikeyic.com/products/signal-relays/hk4100f-dc12v-shg/1209362.html | K2 | 0.3635 | 18.175 | https://www.unikeyic.com/products/signal-relays/hfd16-4-5-zfh3n/102142.html | K2 | 0.1885 | 188.5 | https://www.unikeyic.com/products/signal-relays/1649222-4/33950113.html | K2 | 2.6 | 52000 | https://www.unikeyic.com/products/signal-relays/v23079b1202b301/30598845.html
K3 | 0.3014 | 3.014 | https://www.unikeyic.com/products/signal-relays/hk4100f-dc12v-shg/1209362.html | K3 | 0.3635 | 18.175 | https://www.unikeyic.com/products/signal-relays/hfd16-4-5-zfh3n/102142.html | K3 | 0.1885 | 188.5 | https://www.unikeyic.com/products/signal-relays/1649222-4/33950113.html | K3 | 2.6 | 52000 | https://www.unikeyic.com/products/signal-relays/v23079b1202b301/30598845.html
K4 | 0.3014 | 3.014 | https://www.unikeyic.com/products/signal-relays/hk4100f-dc12v-shg/1209362.html | K4 | 0.3635 | 18.175 | https://www.unikeyic.com/products/signal-relays/hfd16-4-5-zfh3n/102142.html | K4 | 0.1885 | 188.5 | https://www.unikeyic.com/products/signal-relays/1649222-4/33950113.html | K4 | 2.6 | 52000 | https://www.unikeyic.com/products/signal-relays/v23079b1202b301/30598845.html
L1 | 0.1102 | 1.102 | https://www.unikeyic.com/products/power-inductors/slo0630h330mtt/28122264.html | L1 | 0.0912 | 4.56 | https://www.unikeyic.com/products/power-inductors/slo0630h330mtt/28122264.html | L1 | 0.0326 | 32.6 | https://www.unikeyic.com/products/power-inductors/sm7850-330mt/24116420.html | L1 | 0.015 | 300 | https://www.unikeyic.com/products/power-inductors/sm3521-330mt/27973129.html
M1 | 0.0358 | 0.358 | https://www.unikeyic.com/products/motor-driver/l9110s/34426605.html | M1 | 0.0296 | 1.48 | https://www.unikeyic.com/products/motor-driver/gr6212/1005575493.html | M1 | 0.0199 | 19.9 | https://www.unikeyic.com/products/motor-driver/gr6212/1005575493.html | M1 | 0.0114 | 228 | https://www.unikeyic.com/products/motor-driver/sa6208/871310652.html
M2 | 0.0358 | 0.358 | https://www.unikeyic.com/products/motor-driver/l9110s/34426605.html | M2 | 0.0296 | 1.48 | https://www.unikeyic.com/products/motor-driver/gr6212/1005575493.html | M2 | 0.0199 | 19.9 | https://www.unikeyic.com/products/motor-driver/gr6212/1005575493.html | M2 | 0.0114 | 228 | https://www.unikeyic.com/products/motor-driver/sa6208/871310652.html
M3 | 0.0358 | 0.358 | https://www.unikeyic.com/products/motor-driver/l9110s/34426605.html | M3 | 0.0296 | 1.48 | https://www.unikeyic.com/products/motor-driver/gr6212/1005575493.html | M3 | 0.0199 | 19.9 | https://www.unikeyic.com/products/motor-driver/gr6212/1005575493.html | M3 | 0.0114 | 228 | https://www.unikeyic.com/products/motor-driver/sa6208/871310652.html
M5 | 0.0358 | 0.358 | https://www.unikeyic.com/products/motor-driver/l9110s/34426605.html | M5 | 0.0296 | 1.48 | https://www.unikeyic.com/products/motor-driver/gr6212/1005575493.html | M5 | 0.0199 | 19.9 | https://www.unikeyic.com/products/motor-driver/gr6212/1005575493.html | M5 | 0.0114 | 228 | https://www.unikeyic.com/products/motor-driver/sa6208/871310652.html
Q2 | 0.005 | 0.05 | https://www.unikeyic.com/products/bjt/mmbt3904/691147421.html?sku=100300102529011 | Q2 | 0.005 | 0.25 | https://www.unikeyic.com/products/bjt/mmbt3904/691147421.html?sku=100300102529011 | Q2 | 0.003 | 3 | https://www.unikeyic.com/products/bjt/mmbt3904/691147421.html?sku=100300102529011 | Q2 | 0.0033 | 66 | https://www.unikeyic.com/products/bjt/mmbt3904/13701173.html?sku=1003001442654832
Q3 | 0.005 | 0.05 | https://www.unikeyic.com/products/bjt/mmbt3904/691147421.html?sku=100300102529011 | Q3 | 0.005 | 0.25 | https://www.unikeyic.com/products/bjt/mmbt3904/691147421.html?sku=100300102529011 | Q3 | 0.003 | 3 | https://www.unikeyic.com/products/bjt/mmbt3904/691147421.html?sku=100300102529011 | Q3 | 0.0033 | 66 | https://www.unikeyic.com/products/bjt/mmbt3904/13701173.html?sku=1003001442654832
Q4 | 0.005 | 0.05 | https://www.unikeyic.com/products/bjt/mmbt3904/691147421.html?sku=100300102529011 | Q4 | 0.005 | 0.25 | https://www.unikeyic.com/products/bjt/mmbt3904/691147421.html?sku=100300102529011 | Q4 | 0.003 | 3 | https://www.unikeyic.com/products/bjt/mmbt3904/691147421.html?sku=100300102529011 | Q4 | 0.0033 | 66 | https://www.unikeyic.com/products/bjt/mmbt3904/13701173.html?sku=1003001442654832
R2 | 0.0008 | 0.008 | https://www.unikeyic.com/products/surface-mount-resistors/wr06x102jtl/27213648.html | R2 | 0.0006 | 0.03 | https://www.unikeyic.com/products/surface-mount-resistors/scr0603f1k/1464257.html | R2 | 0.0005 | 0.5 | https://www.unikeyic.com/products/surface-mount-resistors/scr0603f1k/1464257.html | R2 | 0.0006 | 12 | https://www.unikeyic.com/products/surface-mount-resistors/rms06jt102/23527918.html
R3 | 0.0008 | 0.008 | https://www.unikeyic.com/products/surface-mount-resistors/wr06x102jtl/27213648.html | R3 | 0.0006 | 0.03 | https://www.unikeyic.com/products/surface-mount-resistors/scr0603f1k/1464257.html | R3 | 0.0005 | 0.5 | https://www.unikeyic.com/products/surface-mount-resistors/scr0603f1k/1464257.html | R3 | 0.0006 | 12 | https://www.unikeyic.com/products/surface-mount-resistors/rms06jt102/23527918.html
R4 | 0.0039 | 0.039 | https://www.unikeyic.com/products/surface-mount-resistors/rk73b1jttd472g/30481446.html | R4 | 0.1495 | 7.475 | https://www.unikeyic.com/products/surface-mount-resistors/crt0603-fx-4701elf/6691641.html | R4 | 0.001 | 1 | https://www.unikeyic.com/products/surface-mount-resistors/rc0603fr-074k7l/5502613.html | R4 | 0.0007 | 14 | https://www.unikeyic.com/products/surface-mount-resistors/rc0603fr-074k7l/5502613.html
R5 | 0.0023 | 0.023 | https://www.unikeyic.com/products/surface-mount-resistors/rc0603fr-13121rl/1596587.html | R5 | 0.0023 | 0.115 | https://www.unikeyic.com/products/surface-mount-resistors/rc0603fr-13121rl/1596587.html | R5 | 0.0023 | 2.3 | https://www.unikeyic.com/products/surface-mount-resistors/rc0603fr-13121rl/1596587.html | R5 | 0.0023 | 46 | https://www.unikeyic.com/products/surface-mount-resistors/rc0603fr-13121rl/1596587.html
R6 | 0.0012 | 0.012 | https://www.unikeyic.com/products/surface-mount-resistors/mr06x2000ftl/34104715.html | R6 | 0.0012 | 0.06 | https://www.unikeyic.com/products/surface-mount-resistors/mr06x2000ftl/34104715.html | R6 | 0.0019 | 1.9 | https://www.unikeyic.com/products/surface-mount-resistors/ac0603fr-07200rl/29991689.html | R6 | 0.0012 | 24 | https://www.unikeyic.com/products/surface-mount-resistors/cq03waj0201t5e/683918389.html
R7 | 0.0008 | 0.008 | https://www.unikeyic.com/products/surface-mount-resistors/wr06x102jtl/27213648.html | R7 | 0.0006 | 0.03 | https://www.unikeyic.com/products/surface-mount-resistors/scr0603f1k/1464257.html | R7 | 0.0005 | 0.5 | https://www.unikeyic.com/products/surface-mount-resistors/scr0603f1k/1464257.html | R7 | 0.0006 | 12 | https://www.unikeyic.com/products/surface-mount-resistors/rms06jt102/23527918.html
R8 | 0.0008 | 0.008 | https://www.unikeyic.com/products/surface-mount-resistors/wr06x102jtl/27213648.html | R8 | 0.0006 | 0.03 | https://www.unikeyic.com/products/surface-mount-resistors/scr0603f1k/1464257.html | R8 | 0.0005 | 0.5 | https://www.unikeyic.com/products/surface-mount-resistors/scr0603f1k/1464257.html | R8 | 0.0006 | 12 | https://www.unikeyic.com/products/surface-mount-resistors/rms06jt102/23527918.html
R9 | 0.033 | 0.33 | https://www.unikeyic.com/products/surface-mount-resistors/ptfr0603b10k0p9/2937877.html | R9 | 0.0273 | 1.365 | https://www.unikeyic.com/products/surface-mount-resistors/ar03btcx1002/28478659.html | R9 | 0.003 | 3 | https://www.unikeyic.com/products/surface-mount-resistors/cr0603-16w-103jt/2487102.html | R9 | 0.003 | 60 | https://www.unikeyic.com/products/surface-mount-resistors/cr0603-16w-103jt/2487102.html
R10 | 0.0039 | 0.039 | https://www.unikeyic.com/products/surface-mount-resistors/rk73b1jttd472g/30481446.html | R10 | 0.1495 | 7.475 | https://www.unikeyic.com/products/surface-mount-resistors/crt0603-fx-4701elf/6691641.html | R10 | 0.001 | 1 | https://www.unikeyic.com/products/surface-mount-resistors/rc0603fr-074k7l/5502613.html | R10 | 0.0007 | 14 | https://www.unikeyic.com/products/surface-mount-resistors/rc0603fr-074k7l/5502613.html
R11 | 1.1654 | 11.654 | https://www.unikeyic.com/products/fans-and-thermal-management/ick-smd-c-10-sa/19099179.html | R11 | 1.1192 | 55.96 | https://www.unikeyic.com/products/fans-and-thermal-management/ick-smd-c-10-sa/19099179.html | R11 | 0.4331 | 433.1 | https://www.unikeyic.com/products/fans-and-thermal-management/thjp0805ast1/22262489.html | R11 | 0.46 | 9200 | https://www.unikeyic.com/products/fans-and-thermal-management/573100d00010g/20312133.html
R12 | 0.0224 | 0.224 | https://www.unikeyic.com/products/surface-mount-resistors/esr03ezpf60r4/26629815.html | R12 | 0.0207 | 1.035 | https://www.unikeyic.com/products/surface-mount-resistors/rt0603brd0760r4l/29063300.html | R12 | 0.0016 | 1.6 | https://www.unikeyic.com/products/surface-mount-resistors/ac0603fr-0760r4l/33884214.html | R12 | 0.0013 | 26 | https://www.unikeyic.com/products/surface-mount-resistors/ac0603fr-0760r4l/33884214.html
R13 | 0.0039 | 0.039 | https://www.unikeyic.com/products/surface-mount-resistors/rk73b1jttd472g/30481446.html | R13 | 0.1495 | 7.475 | https://www.unikeyic.com/products/surface-mount-resistors/crt0603-fx-4701elf/6691641.html | R13 | 0.001 | 1 | https://www.unikeyic.com/products/surface-mount-resistors/rc0603fr-074k7l/5502613.html | R13 | 0.0007 | 14 | https://www.unikeyic.com/products/surface-mount-resistors/rc0603fr-074k7l/5502613.html
R14 | 0.0039 | 0.039 | https://www.unikeyic.com/products/surface-mount-resistors/rk73b1jttd472g/30481446.html | R14 | 0.1495 | 7.475 | https://www.unikeyic.com/products/surface-mount-resistors/crt0603-fx-4701elf/6691641.html | R14 | 0.001 | 1 | https://www.unikeyic.com/products/surface-mount-resistors/rc0603fr-074k7l/5502613.html | R14 | 0.0007 | 14 | https://www.unikeyic.com/products/surface-mount-resistors/rc0603fr-074k7l/5502613.html
R15 | 0.033 | 0.33 | https://www.unikeyic.com/products/surface-mount-resistors/ptfr0603b10k0p9/2937877.html | R15 | 0.0273 | 1.365 | https://www.unikeyic.com/products/surface-mount-resistors/ar03btcx1002/28478659.html | R15 | 0.003 | 3 | https://www.unikeyic.com/products/surface-mount-resistors/cr0603-16w-103jt/2487102.html | R15 | 0.003 | 60 | https://www.unikeyic.com/products/surface-mount-resistors/cr0603-16w-103jt/2487102.html
R16 | 0.033 | 0.33 | https://www.unikeyic.com/products/surface-mount-resistors/ptfr0603b10k0p9/2937877.html | R16 | 0.0273 | 1.365 | https://www.unikeyic.com/products/surface-mount-resistors/ar03btcx1002/28478659.html | R16 | 0.003 | 3 | https://www.unikeyic.com/products/surface-mount-resistors/cr0603-16w-103jt/2487102.html | R16 | 0.003 | 60 | https://www.unikeyic.com/products/surface-mount-resistors/cr0603-16w-103jt/2487102.html
R17 | 0.0224 | 0.224 | https://www.unikeyic.com/products/surface-mount-resistors/esr03ezpf60r4/26629815.html | R17 | 0.0207 | 1.035 | https://www.unikeyic.com/products/surface-mount-resistors/rt0603brd0760r4l/29063300.html | R17 | 0.0016 | 1.6 | https://www.unikeyic.com/products/surface-mount-resistors/ac0603fr-0760r4l/33884214.html | R17 | 0.0013 | 26 | https://www.unikeyic.com/products/surface-mount-resistors/ac0603fr-0760r4l/33884214.html
R18 | 0.0372 | 0.372 | https://www.unikeyic.com/products/surface-mount-resistors/era-3aeb7681v/33626659.html | R18 | 0.018 | 0.9 | https://www.unikeyic.com/products/surface-mount-resistors/rt0603brd077k68l/27672674.html | R18 | 0.0014 | 1.4 | https://www.unikeyic.com/products/surface-mount-resistors/ac0603fr-077k68l/9459382.html | R18 | 0.0011 | 22 | https://www.unikeyic.com/products/surface-mount-resistors/ac0603fr-077k68l/9459382.html
R19 | 0.033 | 0.33 | https://www.unikeyic.com/products/surface-mount-resistors/ptfr0603b10k0p9/2937877.html | R19 | 0.0273 | 1.365 | https://www.unikeyic.com/products/surface-mount-resistors/ar03btcx1002/28478659.html | R19 | 0.003 | 3 | https://www.unikeyic.com/products/surface-mount-resistors/cr0603-16w-103jt/2487102.html | R19 | 0.003 | 60 | https://www.unikeyic.com/products/surface-mount-resistors/cr0603-16w-103jt/2487102.html
R20 | 0.033 | 0.33 | https://www.unikeyic.com/products/surface-mount-resistors/ptfr0603b10k0p9/2937877.html | R20 | 0.0273 | 1.365 | https://www.unikeyic.com/products/surface-mount-resistors/ar03btcx1002/28478659.html | R20 | 0.003 | 3 | https://www.unikeyic.com/products/surface-mount-resistors/cr0603-16w-103jt/2487102.html | R20 | 0.003 | 60 | https://www.unikeyic.com/products/surface-mount-resistors/cr0603-16w-103jt/2487102.html
R21 | 0.033 | 0.33 | https://www.unikeyic.com/products/surface-mount-resistors/ptfr0603b10k0p9/2937877.html | R21 | 0.0273 | 1.365 | https://www.unikeyic.com/products/surface-mount-resistors/ar03btcx1002/28478659.html | R21 | 0.003 | 3 | https://www.unikeyic.com/products/surface-mount-resistors/cr0603-16w-103jt/2487102.html | R21 | 0.003 | 60 | https://www.unikeyic.com/products/surface-mount-resistors/cr0603-16w-103jt/2487102.html
R22 | 0.0372 | 0.372 | https://www.unikeyic.com/products/surface-mount-resistors/era-3aeb7681v/33626659.html | R22 | 0.018 | 0.9 | https://www.unikeyic.com/products/surface-mount-resistors/rt0603brd077k68l/27672674.html | R22 | 0.0014 | 1.4 | https://www.unikeyic.com/products/surface-mount-resistors/ac0603fr-077k68l/9459382.html | R22 | 0.0011 | 22 | https://www.unikeyic.com/products/surface-mount-resistors/ac0603fr-077k68l/9459382.html
R23 | 0.0372 | 0.372 | https://www.unikeyic.com/products/surface-mount-resistors/era-3aeb7681v/33626659.html | R23 | 0.018 | 0.9 | https://www.unikeyic.com/products/surface-mount-resistors/rt0603brd077k68l/27672674.html | R23 | 0.0014 | 1.4 | https://www.unikeyic.com/products/surface-mount-resistors/ac0603fr-077k68l/9459382.html | R23 | 0.0011 | 22 | https://www.unikeyic.com/products/surface-mount-resistors/ac0603fr-077k68l/9459382.html
SW1 | 0.1291 | 1.291 | https://www.unikeyic.com/products/pushbutton-switches/tk-6800-1/30582253.html | SW1 | 0.1062 | 5.31 | https://www.unikeyic.com/products/pushbutton-switches/tk-6800-1/30582253.html | SW1 | 0.1003 | 100.3 | https://www.unikeyic.com/products/pushbutton-switches/xkb8080-z/29657719.html | SW1 | 0.6609 | 13218 | https://www.unikeyic.com/products/pushbutton-switches/tmg1-01/30003257.html
SW2 | 0.1291 | 1.291 | https://www.unikeyic.com/products/pushbutton-switches/tk-6800-1/30582253.html | SW2 | 0.1062 | 5.31 | https://www.unikeyic.com/products/pushbutton-switches/tk-6800-1/30582253.html | SW2 | 0.1003 | 100.3 | https://www.unikeyic.com/products/pushbutton-switches/xkb8080-z/29657719.html | SW2 | 0.6609 | 13218 | https://www.unikeyic.com/products/pushbutton-switches/tmg1-01/30003257.html
SW3 | 0.1291 | 1.291 | https://www.unikeyic.com/products/pushbutton-switches/tk-6800-1/30582253.html | SW3 | 0.1062 | 5.31 | https://www.unikeyic.com/products/pushbutton-switches/tk-6800-1/30582253.html | SW3 | 0.1003 | 100.3 | https://www.unikeyic.com/products/pushbutton-switches/xkb8080-z/29657719.html | SW3 | 0.6609 | 13218 | https://www.unikeyic.com/products/pushbutton-switches/tmg1-01/30003257.html
SW5 | 0.1291 | 1.291 | https://www.unikeyic.com/products/pushbutton-switches/tk-6800-1/30582253.html | SW5 | 0.1062 | 5.31 | https://www.unikeyic.com/products/pushbutton-switches/tk-6800-1/30582253.html | SW5 | 0.1003 | 100.3 | https://www.unikeyic.com/products/pushbutton-switches/xkb8080-z/29657719.html | SW5 | 0.6609 | 13218 | https://www.unikeyic.com/products/pushbutton-switches/tmg1-01/30003257.html
U1 | 0.0856 | 0.856 | https://www.unikeyic.com/products/ldo-controller/lm1117mp-3-3-tr/34334866.html?sku=1003001016206975 | U1 | 0.0681 | 3.405 | https://www.unikeyic.com/products/ldo-controller/lm1117mp-3-3-tr/34334866.html?sku=1003001016206975 | U1 | 0.0528 | 52.8 | https://www.unikeyic.com/products/ldo-controller/lm1117mp-3-3-tr/34334866.html?sku=1003001016206975 | U1 | 0.0998 | 1996 | https://www.unikeyic.com/products/ldo-controller/lm1117mpx-3-3-nopb/34021155.html?sku=1003001442151460
U2 | 0.2022 | 2.022 | https://www.unikeyic.com/products/dc-dc-controller/lm2596s-5-0/34029210.html?sku=1003001028609652 | U2 | 0.1711 | 8.555 | https://www.unikeyic.com/products/motor-driver/drv8871ddarq1/22975465.html?sku=1003001028369650 | U2 | 0.1356 | 135.6 | https://www.unikeyic.com/products/dc-dc-controller/lm2596s-5-0/34029210.html?sku=1003001028609652 | U2 | 0.2742 | 5484 | https://www.unikeyic.com/products/dc-dc-controller/lm2596s-adj/682757583.html?sku=100300107315294
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

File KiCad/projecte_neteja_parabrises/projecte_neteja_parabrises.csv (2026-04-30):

Reference | Qty | Value | DNP | Exclude from BOM | Exclude from Board | Footprint | Datasheet
C1 | 1 | 100n |  |  |  | Capacitor_SMD:C_0805_2012Metric | ~
C2 | 1 | 100n |  |  |  | Capacitor_SMD:C_0805_2012Metric | ~
C10 | 1 | 100n |  |  |  | Capacitor_SMD:C_0805_2012Metric | ~
C16 | 1 | 100n |  |  |  | Capacitor_SMD:C_0805_2012Metric | ~
C3 | 1 | 20p |  |  |  | Capacitor_SMD:C_0805_2012Metric | ~
C4 | 1 | 20p |  |  |  | Capacitor_SMD:C_0805_2012Metric | ~
C5 | 1 | 1u |  |  |  | Capacitor_SMD:C_0805_2012Metric | ~
C6 | 1 | 1u |  |  |  | Capacitor_SMD:C_0805_2012Metric | ~
C7 | 1 | 1u |  |  |  | Capacitor_SMD:C_0805_2012Metric | ~
C8 | 1 | 1u |  |  |  | Capacitor_SMD:C_0805_2012Metric | ~
C9 | 1 | 1u |  |  |  | Capacitor_SMD:C_0805_2012Metric | ~
C11 | 1 | 680uF |  |  |  | Capacitor_SMD:C_0805_2012Metric | ~
C12 | 1 | 220uF |  |  |  | Capacitor_SMD:C_0805_2012Metric | ~
C13 | 1 | 10uF |  |  |  | Capacitor_THT:CP_Radial_D5.0mm_P2.50mm
C14 | 1 | 10uF |  |  |  | Capacitor_THT:CP_Radial_D5.0mm_P2.50mm
C15 | 1 | 100uF |  |  |  | Capacitor_THT:CP_Radial_D5.0mm_P2.50mm
C17 | 1 | 10p |  |  |  | Capacitor_SMD:C_0805_2012Metric | ~
C19 | 1 | 100p |  |  |  | Capacitor_SMD:C_0805_2012Metric | ~
D2 | 1 | LED |  |  |  | LED_SMD:LED_0805_2012Metric_Pad1.15x1.40mm_HandSolder | ~
D3 | 1 | SM6T24A |  |  |  | Diode_SMD:D_SMB | https://www.st.com/resource/en/datasheet/sm6t.pdf
D4 | 1 | D |  |  |  | Diode_SMD:D_0201_0603Metric_Pad0.64x0.40mm_HandSolder | ~
D5 | 1 | D |  |  |  | Diode_SMD:D_0201_0603Metric_Pad0.64x0.40mm_HandSolder | ~
D6 | 1 | D |  |  |  | Diode_SMD:D_0201_0603Metric_Pad0.64x0.40mm_HandSolder | ~
FB1 | 1 | FerriteBead |  |  |  | Ferrite_THT:LairdTech_28C0236-0JW-10 | ~
FINALCARRERA1 | 1 | SW_SPDT |  |  |  | Button_Switch_THT:SW_XKB_DM1-16UC-1 | ~
FINALCARRERA2 | 1 | SW_SPDT |  |  |  | Button_Switch_THT:SW_XKB_DM1-16UC-1 | ~
J1 | 1 | Conn_01x05_Pin |  |  |  | Connector_PinHeader_2.54mm:PinHeader_1x05_P2.54mm_Vertical | ~
J2 | 1 | DE9_Pins |  |  |  | Connector_Dsub:DSUB-9_Pins_Horizontal_P2.77x2.84mm_EdgePinOffset9.40mm | ~
J3 | 1 | DE9_Pins |  |  |  | Connector_Dsub:DSUB-9_Pins_Horizontal_P2.77x2.84mm_EdgePinOffset9.40mm | ~
J4 | 1 | Conn_01x02_Pin |  |  |  | Connector_PinHeader_2.54mm:PinHeader_1x02_P2.54mm_Vertical | ~
JP1 | 1 | Jumper_3_Bridged12 |  | Excluded from BOM |  | Connector_PinHeader_2.54mm:PinHeader_1x03_P2.54mm_Vertical | ~
K2 | 1 | Fujitsu_FTR-LYAA005x |  |  |  | Relay_THT:Relay_SPST-NO_Fujitsu_FTR-LYAA005x_FormA_Vertical | https://www.fujitsu.com/sg/imagesgig5/ftr-ly.pdf
K3 | 1 | Fujitsu_FTR-LYAA005x |  |  |  | Relay_THT:Relay_SPST-NO_Fujitsu_FTR-LYAA005x_FormA_Vertical | https://www.fujitsu.com/sg/imagesgig5/ftr-ly.pdf
K4 | 1 | Fujitsu_FTR-LYAA005x |  |  |  | Relay_THT:Relay_SPST-NO_Fujitsu_FTR-LYAA005x_FormA_Vertical | https://www.fujitsu.com/sg/imagesgig5/ftr-ly.pdf

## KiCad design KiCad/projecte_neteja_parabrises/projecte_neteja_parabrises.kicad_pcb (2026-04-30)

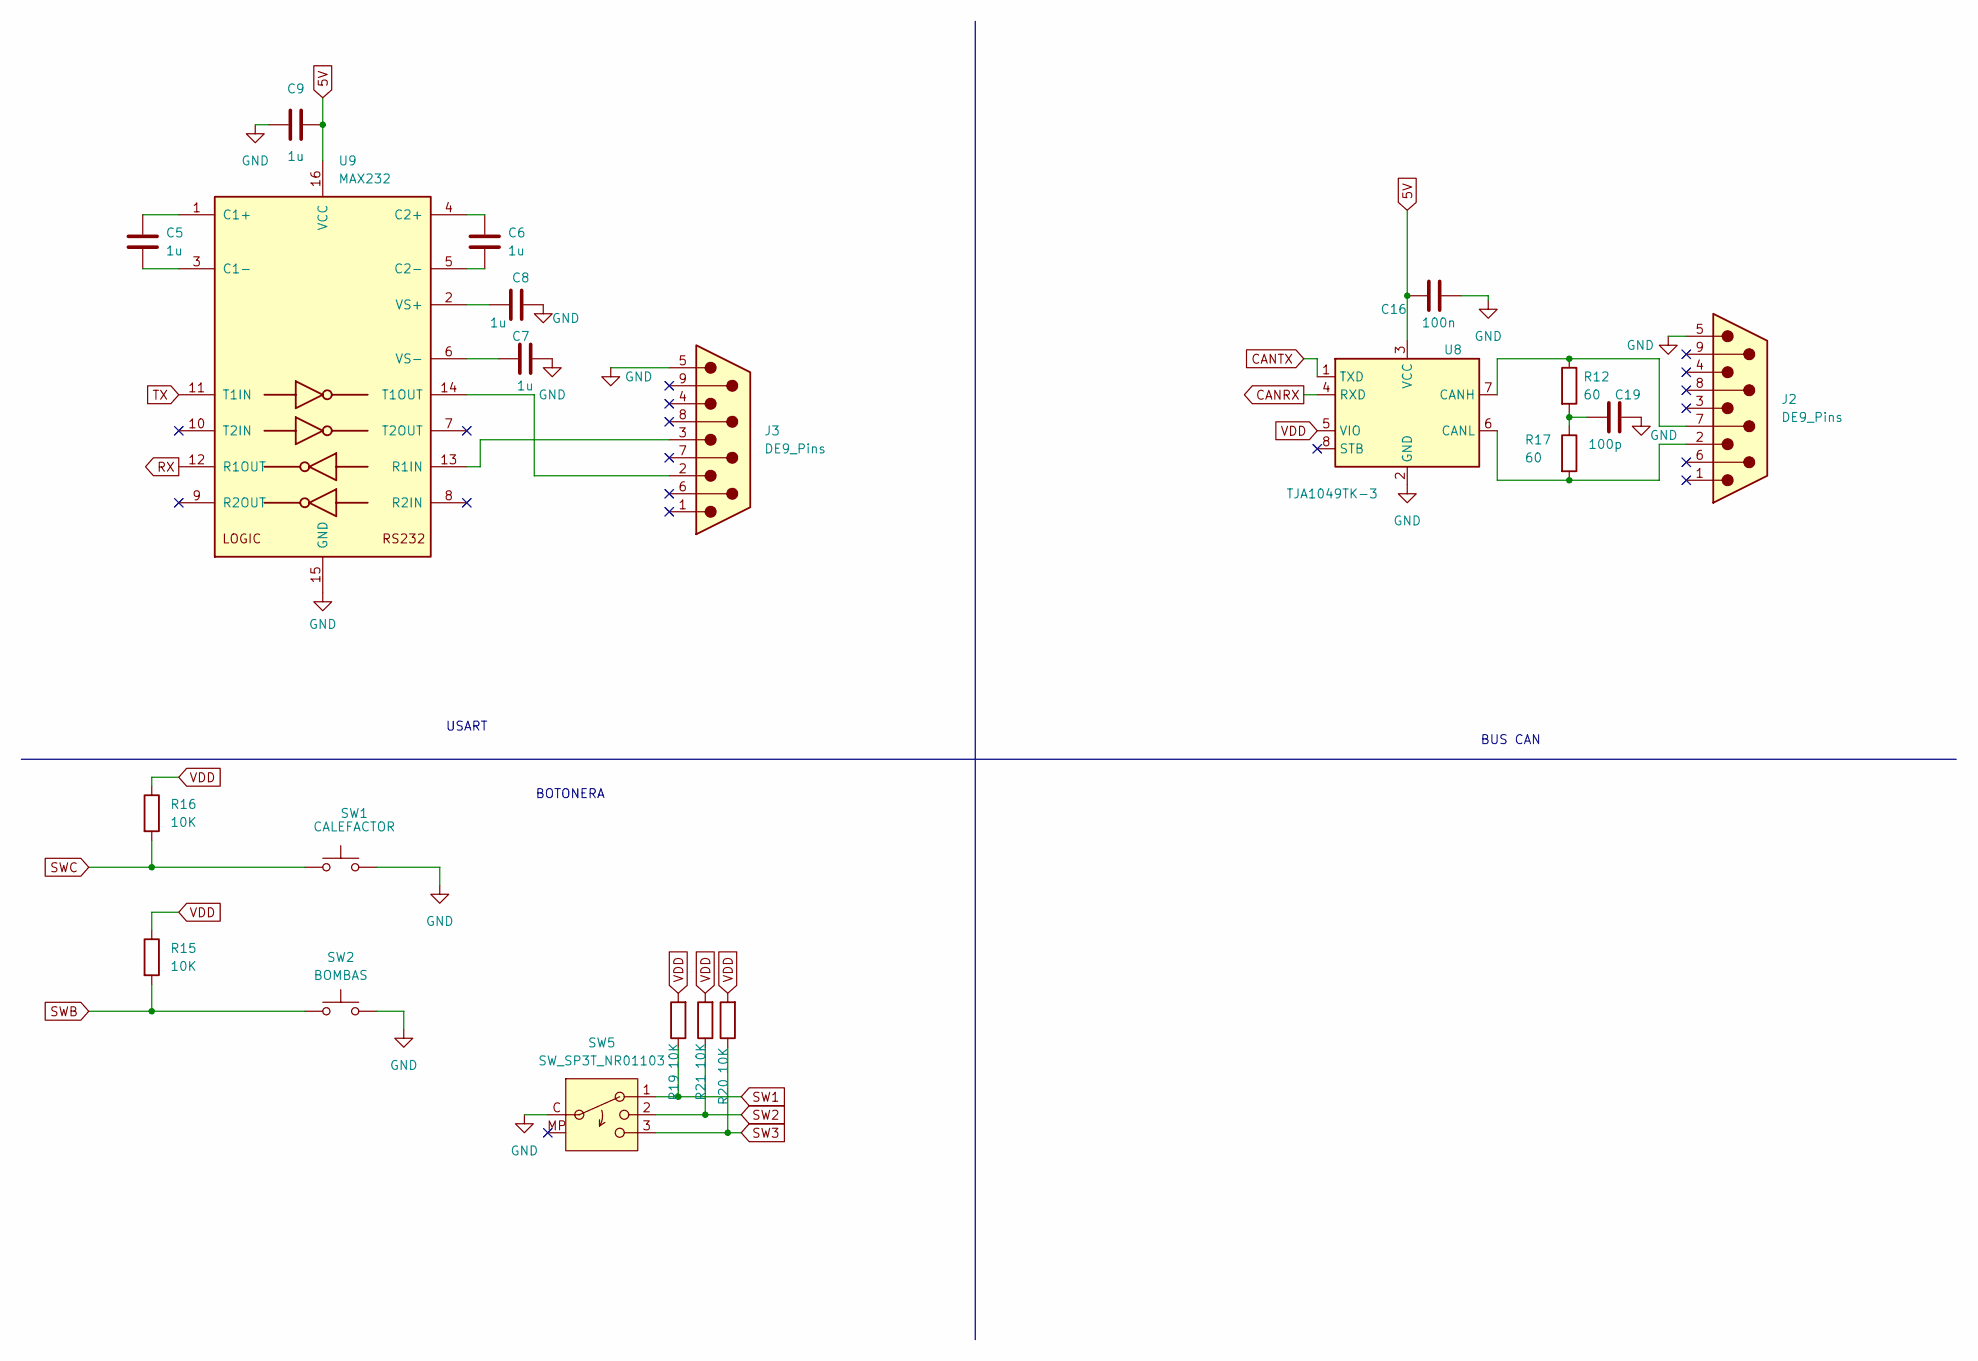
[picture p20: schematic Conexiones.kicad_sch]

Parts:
C5, C6, C7, C8, C9: 1u; C_0805_2012Metric
C16: 100n; C_0805_2012Metric
C19: 100p; C_0805_2012Metric
J2, J3: DE9_Pins; DSUB-9_Pins_Horizontal_P2.77x2.84mm_EdgePinOffset9.40mm
R12, R17: 60; R_0201_0603Metric_Pad0.64x0.40mm_HandSolder
R15, R16: 10K; R_0603_1608Metric_Pad0.98x0.95mm_HandSolder
R19, R20, R21: 10K; R_0201_0603Metric_Pad0.64x0.40mm_HandSolder
SW1: CALEFACTOR; SW_Push_SPST_NO_Alps_SKRK
SW2: BOMBAS; SW_Push_SPST_NO_Alps_SKRK
SW5: SW_SP3T_NR01103; SW_NKK_NR01
U8: TJA1049TK-3; HVSON-8-1EP_3x3mm_P0.65mm_EP1.6x2.4mm
U9: MAX232; JEITA_SOIC-16_3.9x9.9mm_P1.27mm

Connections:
5V: C9.2, C16.1, U8.3 (VCC), U9.16 (VCC); also elsewhere on the board
CANRX: U8.4 (RXD); also elsewhere on the board
CANTX: U8.1 (TXD); also elsewhere on the board
GND: C7.1, C8.1, C9.1, C16.2, C19.2, J2.5, J3.5, SW1.2, SW2.2, SW5.C (Common), U8.2 (GND), U8.9 (GND), U9.15 (GND); also elsewhere on the board
unnamed: C19.1, R12.2, R17.1
unnamed: J2.7, R12.1, U8.7 (CANH)
unnamed: J2.2, R17.2, U8.6 (CANL)
unnamed: C5.1, U9.1 (C1+)
unnamed: C5.2, U9.3 (C1-)
unnamed: C6.1, U9.4 (C2+)
unnamed: C6.2, U9.5 (C2-)
unnamed: J3.3, U9.13 (R1IN)
unnamed: J3.2, U9.14 (T1OUT)
unnamed: C8.2, U9.2 (VS+)
unnamed: C7.2, U9.6 (VS-)
RX: U9.12 (R1OUT); also elsewhere on the board
SW1: R19.1, SW5.1; also elsewhere on the board
SW2: R21.1, SW5.2; also elsewhere on the board
SW3: R20.1, SW5.3; also elsewhere on the board
SWB: R15.2, SW2.1; also elsewhere on the board
SWC: R16.2, SW1.1; also elsewhere on the board
TX: U9.11 (T1IN); also elsewhere on the board
VDD: R15.1, R16.1, R19.2, R20.2, R21.2, U8.5 (VIO); also elsewhere on the board

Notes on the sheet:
BUS CAN
USART
BOTONERA

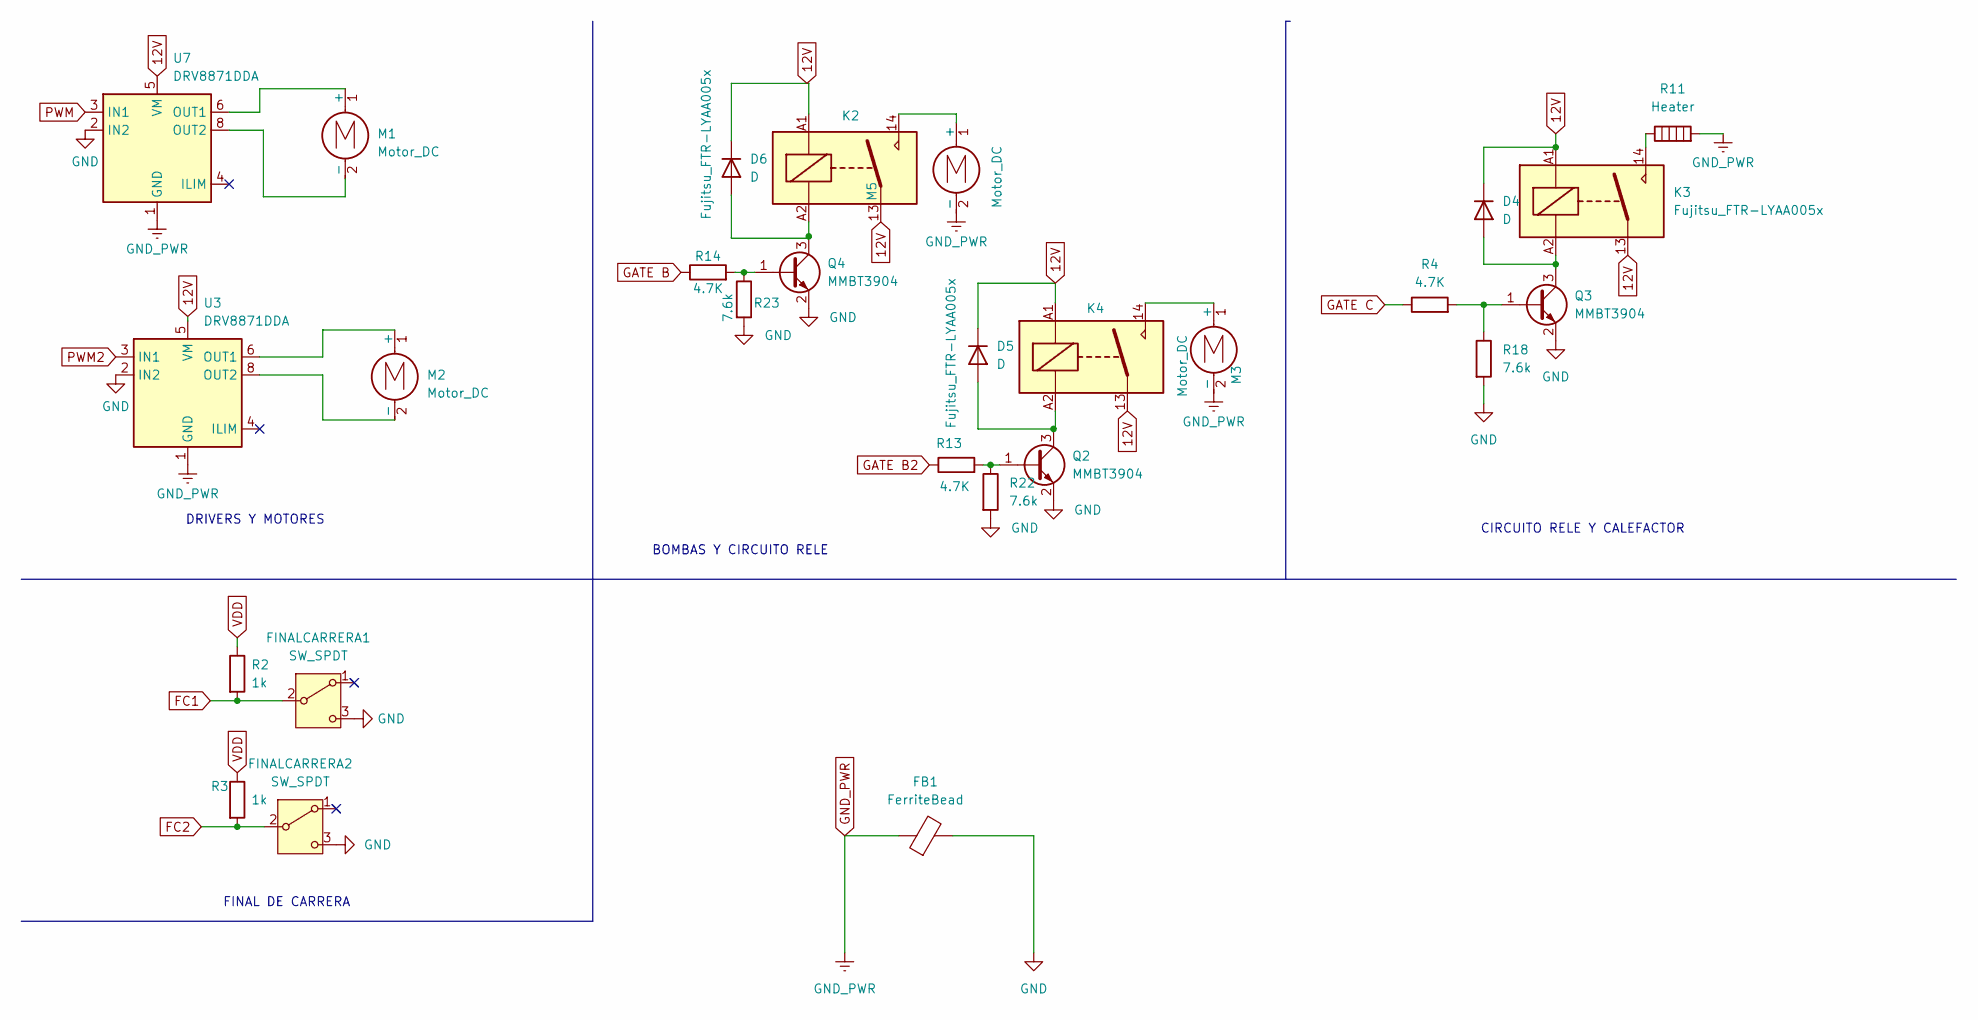
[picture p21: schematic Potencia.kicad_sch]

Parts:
D4, D5, D6: D; D_0201_0603Metric_Pad0.64x0.40mm_HandSolder
FB1: FerriteBead; LairdTech_28C0236-0JW-10
FINALCARRERA1, FINALCARRERA2: SW_SPDT; SW_XKB_DM1-16UC-1
K2, K3, K4: Fujitsu_FTR-LYAA005x; Relay_SPST-NO_Fujitsu_FTR-LYAA005x_FormA_Vertical
M1, M2, M3, M5: Motor_DC; TerminalBlock_MaiXu_MX126-5.0-02P_1x02_P5.00mm
Q2, Q3, Q4: MMBT3904; SOT-23
R2, R3: 1k; R_0603_1608Metric_Pad0.98x0.95mm_HandSolder
R4, R13, R14: 4.7K; R_0603_1608Metric_Pad0.98x0.95mm_HandSolder
R11: Heater; R_2512_6332Metric_Pad1.40x3.35mm_HandSolder
R18, R22, R23: 7.6k; R_0603_1608Metric_Pad0.98x0.95mm_HandSolder
U3, U7: DRV8871DDA; Texas_HTSOP-8-1EP_3.9x4.9mm_P1.27mm_EP2.95x4.9mm_Mask2.4x3.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

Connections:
12V: D4.1 (K), D5.1 (K), D6.1 (K), K2.13, K2.A1, K3.13, K3.A1, K4.13, K4.A1, U3.5 (VM), U7.5 (VM); also elsewhere on the board
FC1: FINALCARRERA1.2 (B), R2.2; also elsewhere on the board
FC2: FINALCARRERA2.2 (B), R3.2; also elsewhere on the board
GATE B: R14.1; also elsewhere on the board
GATE B2: R13.1; also elsewhere on the board
GATE C: R4.1; also elsewhere on the board
GND: FB1.2, FINALCARRERA1.3 (C), FINALCARRERA2.3 (C), Q2.2 (E), Q3.2 (E), Q4.2 (E), R18.2, R22.2, R23.2, U3.2 (IN2), U7.2 (IN2); also elsewhere on the board
GND_PWR: FB1.1, M3.2 (-), M5.2 (-), R11.2, U3.1 (GND), U3.7 (GND), U3.9 (GND), U7.1 (GND), U7.7 (GND), U7.9 (GND)
unnamed: D4.2 (A), K3.A2, Q3.3 (C)
unnamed: D5.2 (A), K4.A2, Q2.3 (C)
unnamed: D6.2 (A), K2.A2, Q4.3 (C)
unnamed: K3.14, R11.1
unnamed: M1.1 (+), U7.6 (OUT1)
unnamed: M1.2 (-), U7.8 (OUT2)
unnamed: M2.1 (+), U3.6 (OUT1)
unnamed: M2.2 (-), U3.8 (OUT2)
unnamed: K4.14, M3.1 (+)
unnamed: K2.14, M5.1 (+)
unnamed: Q2.1 (B), R13.2, R22.1
unnamed: Q3.1 (B), R4.2, R18.1
unnamed: Q4.1 (B), R14.2, R23.1
PWM: U7.3 (IN1); also elsewhere on the board
PWM2: U3.3 (IN1); also elsewhere on the board
VDD: R2.1, R3.1; also elsewhere on the board

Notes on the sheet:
FINAL DE CARRERA
DRIVERS Y MOTORES
BOMBAS Y CIRCUITO RELE
CIRCUITO RELE Y CALEFACTOR

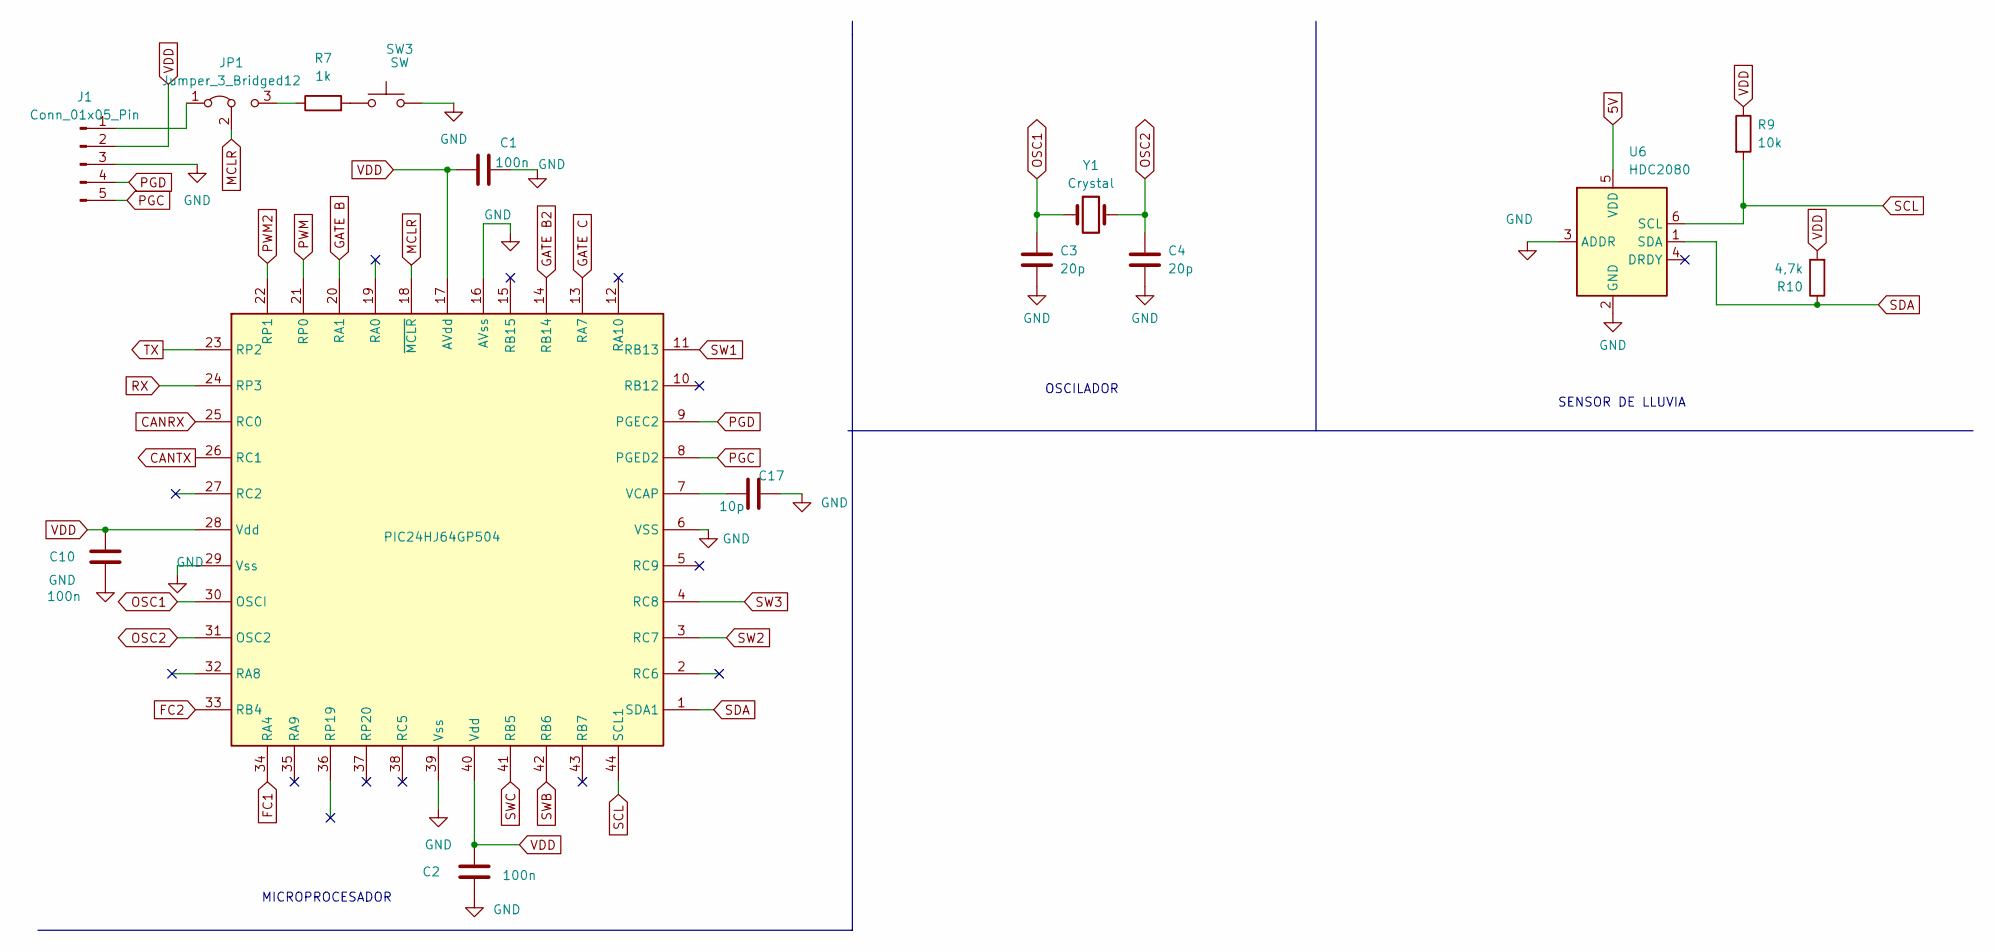
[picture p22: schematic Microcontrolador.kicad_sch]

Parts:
C1, C2, C10: 100n; C_0805_2012Metric
C3, C4: 20p; C_0805_2012Metric
C17: 10p; C_0805_2012Metric
J1: Conn_01x05_Pin; PinHeader_1x05_P2.54mm_Vertical
JP1: Jumper_3_Bridged12; PinHeader_1x03_P2.54mm_Vertical
R7: 1k; R_0603_1608Metric_Pad0.98x0.95mm_HandSolder
R9: 10k; R_0603_1608Metric_Pad0.98x0.95mm_HandSolder
R10: 4,7k; R_0603_1608Metric_Pad0.98x0.95mm_HandSolder
SW3: SW; SW_Push_SPST_NO_Alps_SKRK
U4: PIC24HJ64GP504; QFN-44-1EP_7x7mm_P0.5mm_EP5.2x5.2mm
U6: HDC2080; Texas_S-PWSON-N6-HDC2080
Y1: Crystal; Crystal_SMD_EuroQuartz_EQ161-2Pin_3.2x1.5mm_HandSoldering

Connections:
5V: U6.5 (VDD); also elsewhere on the board
CANRX: U4.25 (RC0); also elsewhere on the board
CANTX: U4.26 (RC1); also elsewhere on the board
FC1: U4.34 (RA4); also elsewhere on the board
FC2: U4.33 (RB4); also elsewhere on the board
GATE B: U4.20 (RA1); also elsewhere on the board
GATE B2: U4.14 (RB14); also elsewhere on the board
GATE C: U4.13 (RA7); also elsewhere on the board
GND: C1.1, C2.1, C3.2, C4.2, C10.1, C17.2, J1.3, SW3.2, U4.6 (VSS), U4.16 (AVss), U4.29 (Vss), U4.39 (Vss), U6.2 (GND), U6.3 (ADDR); also elsewhere on the board
MCLR: JP1.2 (C), U4.18 (~MCLR)
unnamed: J1.1, JP1.1 (A)
unnamed: JP1.3 (B), R7.1
unnamed: R7.2, SW3.1
unnamed: C17.1, U4.7 (VCAP)
OSC1: C3.1, U4.30 (OSCI), Y1.1
OSC2: C4.1, U4.31 (OSC2), Y1.2
PGC: J1.5, U4.8 (PGED2)
PGD: J1.4, U4.9 (PGEC2)
PWM: U4.21 (RP0); also elsewhere on the board
PWM2: U4.22 (RP1); also elsewhere on the board
RX: U4.24 (RP3); also elsewhere on the board
SCL: R9.2, U4.44 (SCL1), U6.6 (SCL)
SDA: R10.1, U4.1 (SDA1), U6.1 (SDA)
SW1: U4.11 (RB13); also elsewhere on the board
SW2: U4.3 (RC7); also elsewhere on the board
SW3: U4.4 (RC8); also elsewhere on the board
SWB: U4.42 (RB6); also elsewhere on the board
SWC: U4.41 (RB5); also elsewhere on the board
TX: U4.23 (RP2); also elsewhere on the board
VDD: C1.2, C2.2, C10.2, J1.2, R9.1, R10.2, U4.17 (AVdd), U4.28 (Vdd), U4.40 (Vdd); also elsewhere on the board

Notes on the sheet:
SENSOR DE LLUVIA
OSCILADOR
MICROPROCESADOR

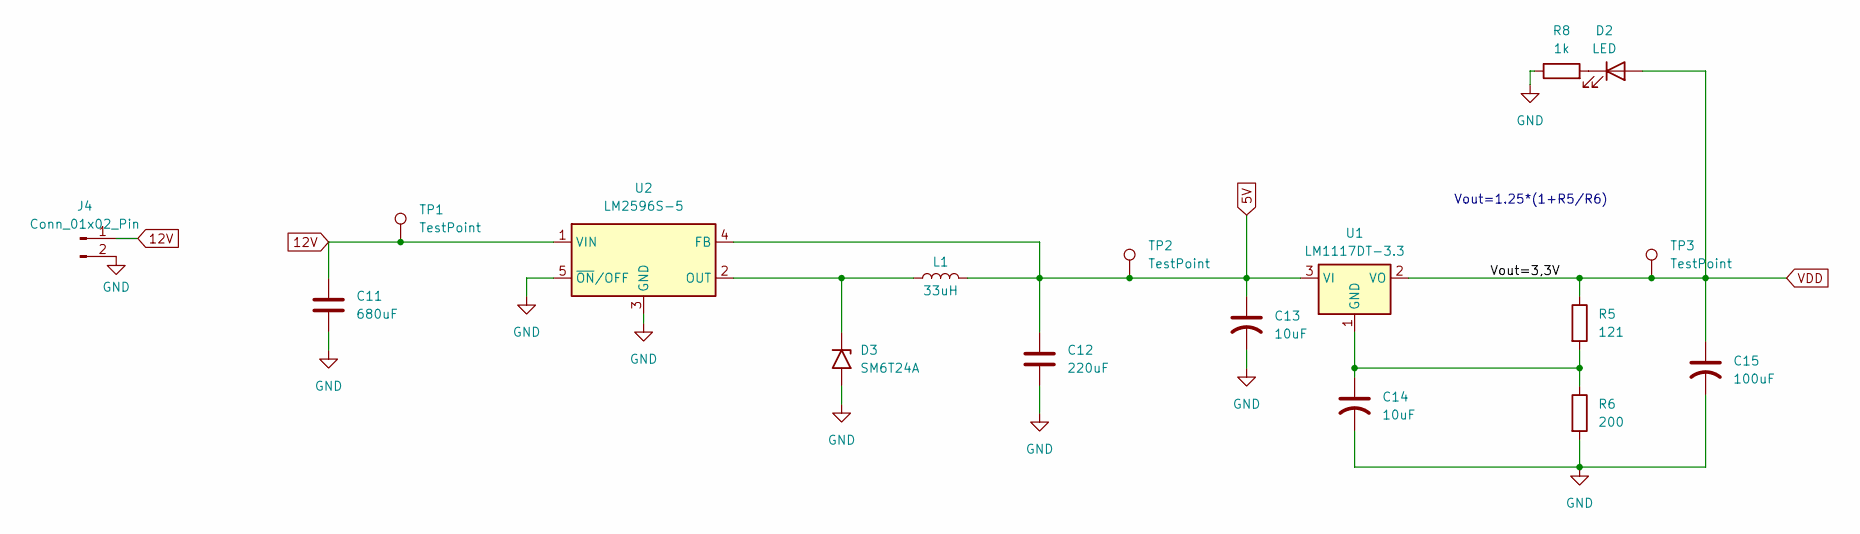
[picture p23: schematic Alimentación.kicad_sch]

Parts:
C11: 680uF; C_0805_2012Metric
C12: 220uF; C_0805_2012Metric
C13, C14: 10uF; CP_Radial_D5.0mm_P2.50mm
C15: 100uF; CP_Radial_D5.0mm_P2.50mm
D2: LED; LED_0805_2012Metric_Pad1.15x1.40mm_HandSolder
D3: SM6T24A; D_SMB
J4: Conn_01x02_Pin; PinHeader_1x02_P2.54mm_Vertical
L1: 33uH; L_0603_1608Metric_Pad1.05x0.95mm_HandSolder
R5: 121; R_0603_1608Metric_Pad0.98x0.95mm_HandSolder
R6: 200; R_0603_1608Metric_Pad0.98x0.95mm_HandSolder
R8: 1k; R_0603_1608Metric_Pad0.98x0.95mm_HandSolder
TP1, TP2, TP3: TestPoint; TestPoint_Keystone_5015_Micro_Mini
U1: LM1117DT-3.3; TO-252-3_TabPin2
U2: LM2596S-5; TO-263-5_TabPin3

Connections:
5V: C12.1, C13.1, L1.2, TP2.1, U1.3 (VI), U2.4 (FB); also elsewhere on the board
12V: C11.1, J4.1, TP1.1, U2.1 (VIN); also elsewhere on the board
GND: C11.2, C12.2, C13.2, C14.2, C15.2, D3.2 (A2), J4.2, R6.2, R8.1, U2.3 (GND), U2.5 (~ON/OFF); also elsewhere on the board
unnamed: D2.1 (K), R8.2
unnamed: D3.1 (A1), L1.1, U2.2 (OUT)
unnamed: C14.1, R5.2, R6.1, U1.1 (GND)
VDD: C15.1, D2.2 (A), R5.1, TP3.1, U1.2 (VO); also elsewhere on the board

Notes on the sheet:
Vout=1.25*(1+R5/R6)

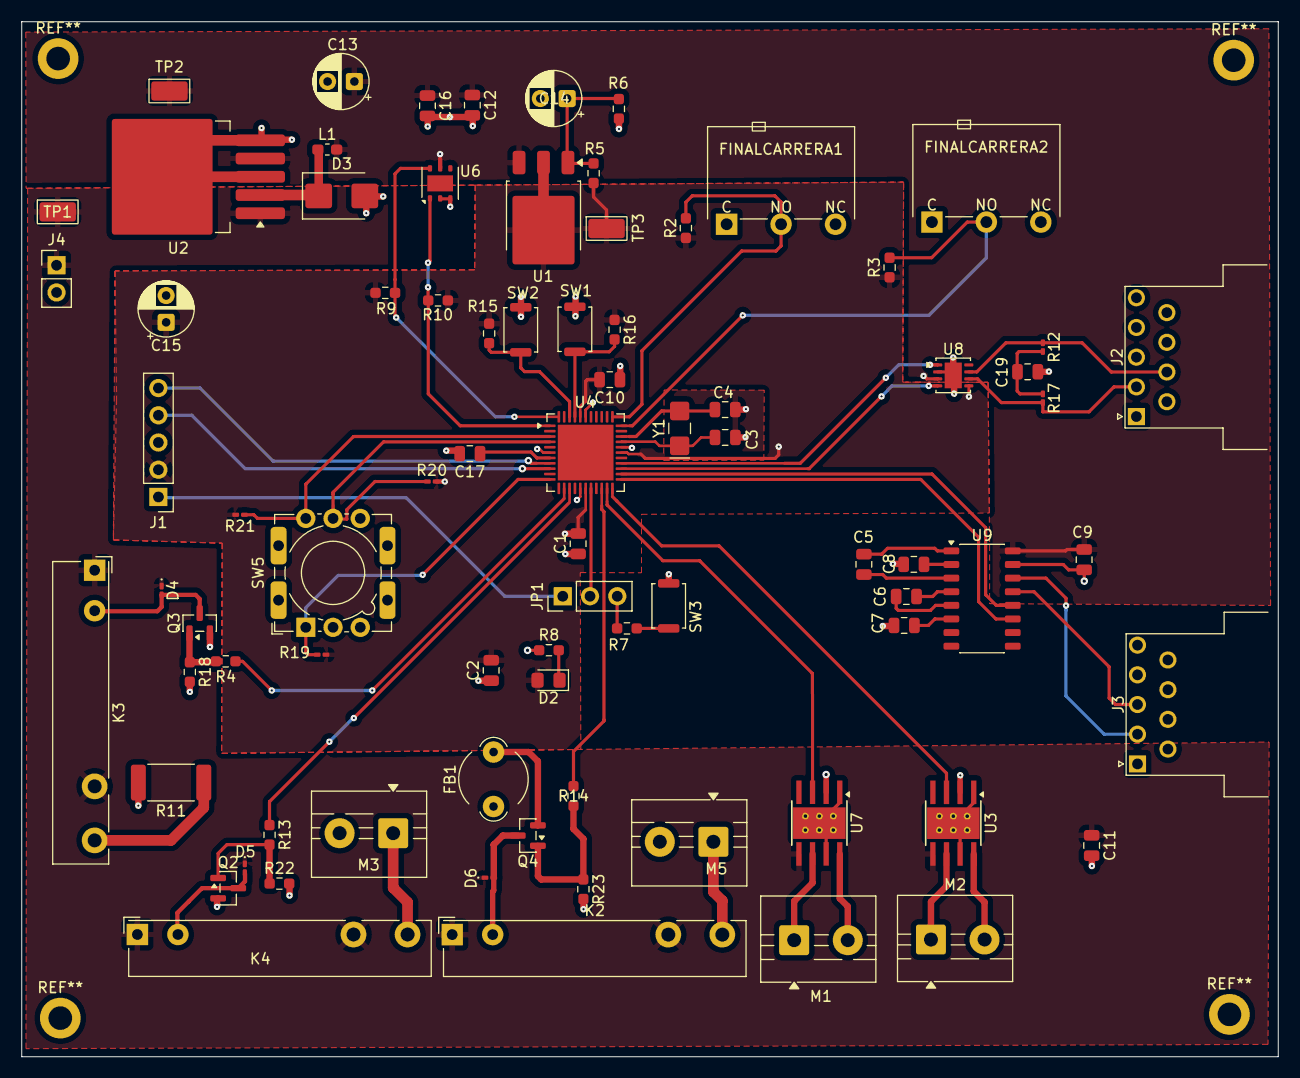
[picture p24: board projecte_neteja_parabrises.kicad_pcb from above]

Board: 2 copper layers, 117.2 x 96.5 mm, 80 parts (0 on the bottom side), 59 nets.

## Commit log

2026-03-16 projecte kicad
    [projecte_neteja_parabrises.kicad_pcb, projecte_neteja_parabrises.kicad_sch]
2026-03-18 Prueba Potencia
    [Potencia.kicad_sch]
2026-03-18 Potencia actualizada
    [Microcontrolador.kicad_sch, Potencia.kicad_sch]
2026-03-18 error raro
    [Microcontrolador.kicad_sch]
2026-03-18 BOMBAS Y FINAL DEL CARRERA
    [Potencia.kicad_sch]
2026-03-18 POTENCIA ACABADA
    [Potencia.kicad_sch]
2026-03-18 V1 SCH
    [Microcontrolador.kicad_sch]
2026-03-19 SCH V1
    [Alimentación.kicad_sch, Botonera.kicad_sch, Microcontrolador.kicad_sch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]
2026-03-19 SCH ALIMETNACION
    [Botonera.kicad_sch]
2026-03-19 alimentacio millora
    [Alimentación.kicad_sch]
2026-03-19 alimentacio acabada
    [Alimentación.kicad_sch]
2026-03-19 UART ACABADO
    [Microcontrolador.kicad_sch, Potencia.kicad_sch]
2026-03-19 alimentacio arreglada
    [Alimentación.kicad_sch]
2026-03-19 MICRO ACTUALIZADA
    [Microcontrolador.kicad_sch, Potencia.kicad_sch]
2026-03-20 ESQUEMATICO V2
    [Alimentación.kicad_sch, Botonera.kicad_sch, Microcontrolador.kicad_sch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]
2026-03-24 Error de nombres solucionado
    [Alimentación.kicad_sch, Microcontrolador.kicad_sch, Potencia.kicad_sch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]
2026-03-25 millora alimentacio
    [Alimentación.kicad_sch]
2026-03-25 Actualización huellas
    [Alimentación.kicad_sch, Microcontrolador.kicad_sch, Potencia.kicad_sch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]
2026-03-25 huella bateria
    [Alimentación.kicad_sch]
2026-03-25 huella c electrolitica
    [Alimentación.kicad_sch]
2026-03-26 Placa definitiva
    [Microcontrolador.kicad_sch, Potencia.kicad_sch, projecte_neteja_parabrises.kicad_pcb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]
2026-03-26 readme foto
    [Potencia.kicad_sch]
2026-03-26 millora botonera
    [Potencia.kicad_sch, untitled.kicad_sch]
2026-03-26 Actualizacion errores
    [Microcontrolador.kicad_sch, Potencia.kicad_sch, projecte_neteja_parabrises.kicad_pcb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]
2026-03-26 detector lluvia
    [Potencia.kicad_sch, untitled.kicad_sch]
2026-03-26 potencia cambios
    [Alimentación.kicad_sch, Potencia.kicad_sch]
2026-04-01 POTENCIA GND
    [Microcontrolador.kicad_sch, Potencia.kicad_sch, untitled.kicad_sch]
2026-04-01 huella ferrita
    [Potencia.kicad_sch, untitled.kicad_sch]
2026-04-06 actualizacion componentes placa
    [projecte_neteja_parabrises.kicad_pcb]
2026-04-09 placements restantes
    [projecte_neteja_parabrises.kicad_pcb]
2026-04-09 pcb placement
    [Microcontrolador.kicad_sch, Potencia.kicad_sch, projecte_neteja_parabrises.kicad_pcb]
2026-04-16 test points
    [projecte_neteja_parabrises.kicad_pcb]
2026-04-16 actualitzacio pcb
    [Microcontrolador.kicad_sch, projecte_neteja_parabrises.kicad_pcb]
2026-04-17 pcb cristal
    [projecte_neteja_parabrises.kicad_pcb]
2026-04-22 vias pcb
    [Microcontrolador.kicad_sch, projecte_neteja_parabrises.kicad_pcb]
